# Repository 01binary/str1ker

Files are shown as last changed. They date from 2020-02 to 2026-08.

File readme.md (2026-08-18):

# Str1ker: The Drumming Mech

> [Str1ker](https://www.01binary.us/projects/drumming-robot/) is a human size, open-source mech integrated with Robot Operating System.

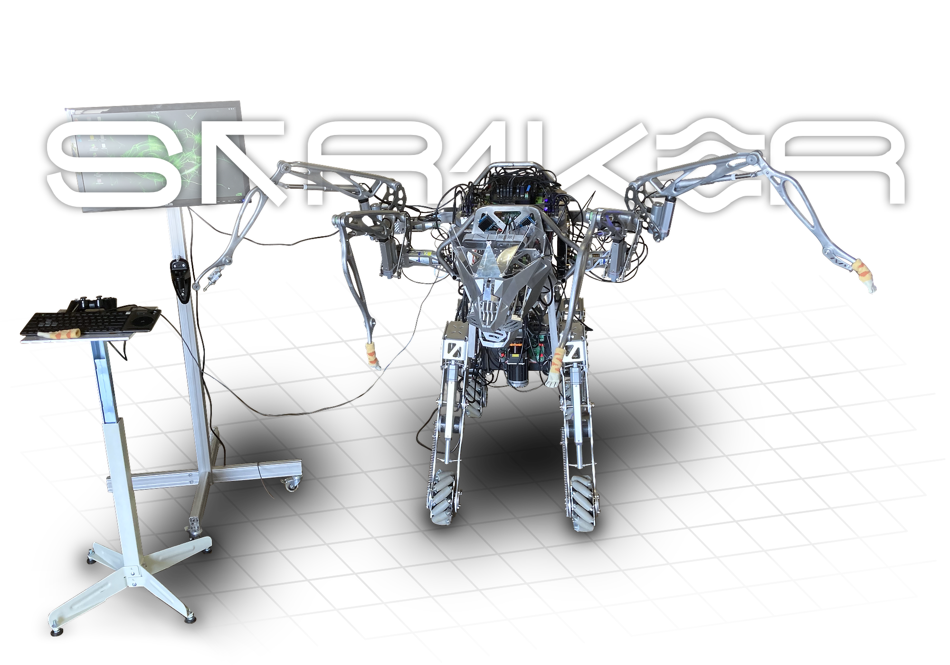
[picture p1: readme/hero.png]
body


## Overview

Striker is a human-scale teleoperated mech built with metal casting, CNC machining, 3D printing, sheet metal parts, tube frame chassis, and pre-made components.

This open-source educational project features custom electronics and [Robot Operating System](https://www.ros.org/) integration, demonstrating how to design and build a large robot that combines mobility, sensing, and manipulation.

> See the [presentation](https://docs.google.com/presentation/d/125Y3McedITN_gVbnEh7SqTWY80QppUtimkaTmMLYEUg/edit?usp=sharing) about the robot at August 2026 [Portland Area Robotics Society](https://portlandrobotics.org/home.php?link_id=1) meeting.

| | | |
|-|-|-|
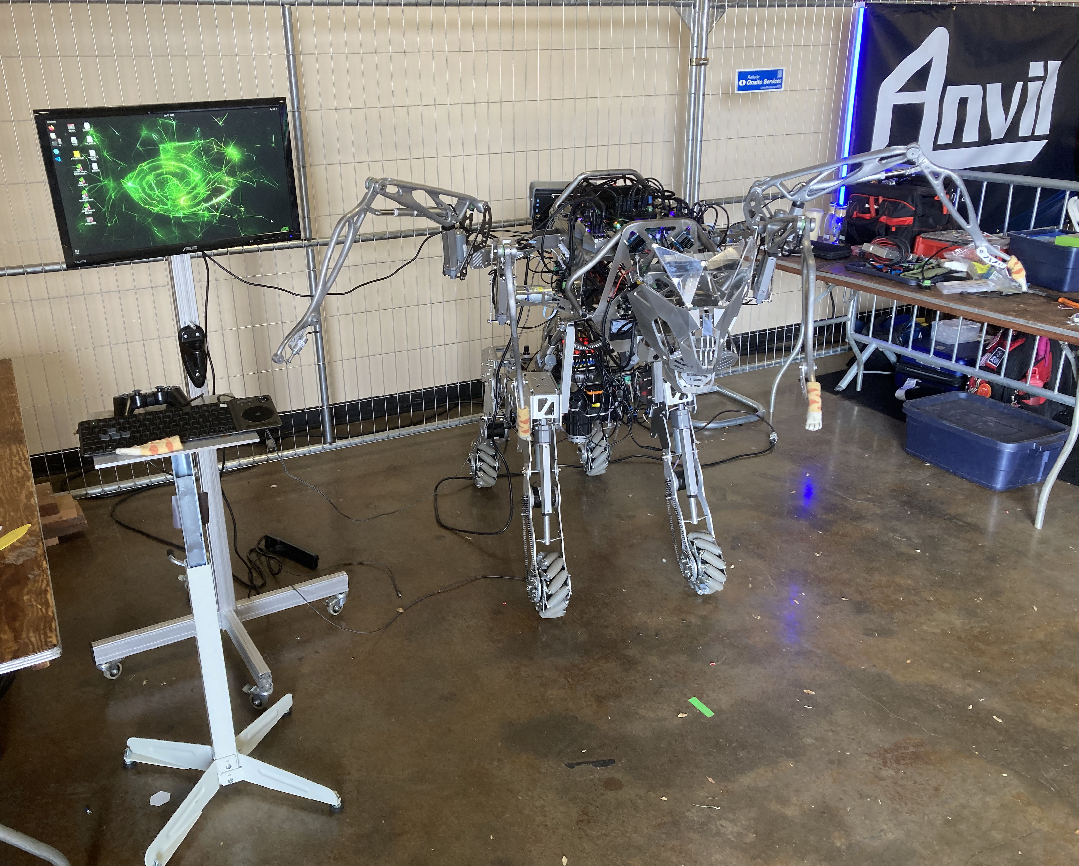
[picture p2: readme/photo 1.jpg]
Front of the robot
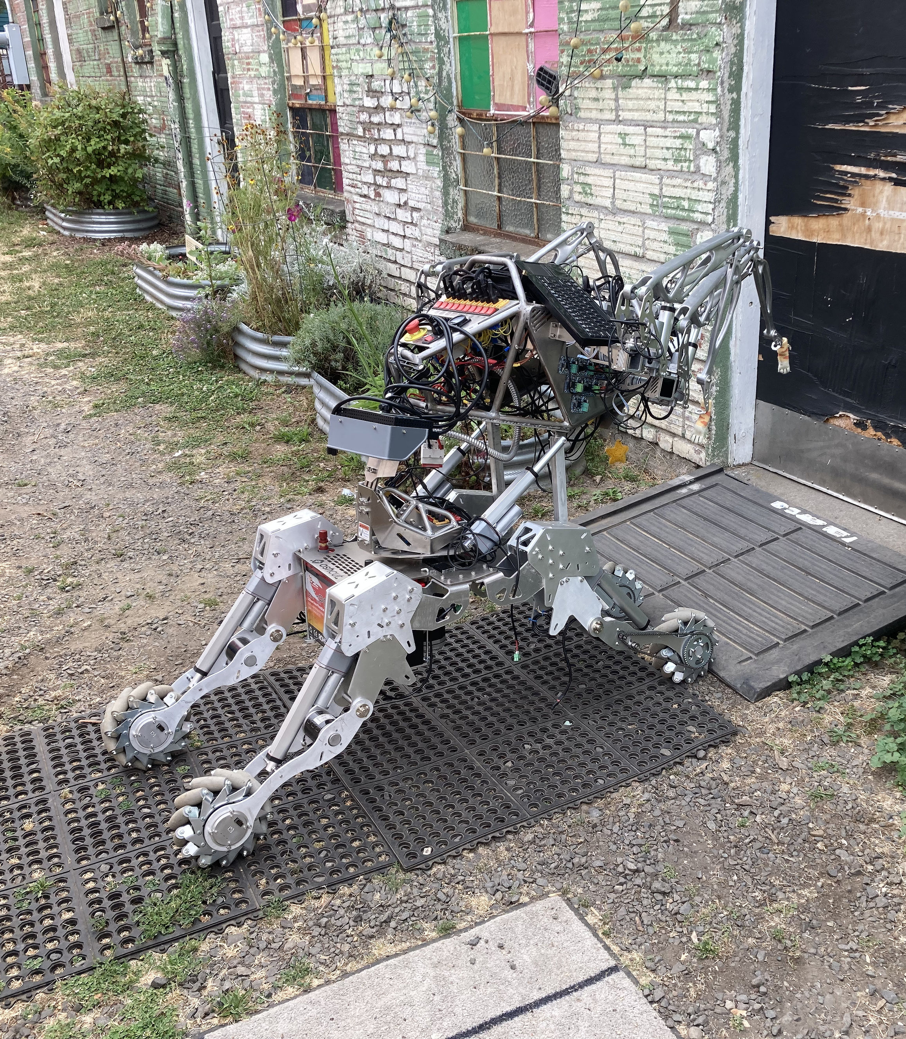
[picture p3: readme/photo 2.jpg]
Robot rolling up a ramp
||Back of the robot||

The robot moves on a mecanum base, articulates its head and arms, and visualizes live lidar and RGB-D perception in Robot Visualization tool ([RViz](https://wiki.ros.org/rviz/Tutorials)).

The arms terminate in percussive end-effectors, designed for future live drum performance.

More details on [my blog](https://www.01binary.us/projects/drumming-robot/) and media on [instagram](https://www.instagram.com/01binaryus/). Say hello at the next [Portland Area Robotics Society](https://portlandrobotics.org/home.php?link_id=1) monthly meetup!

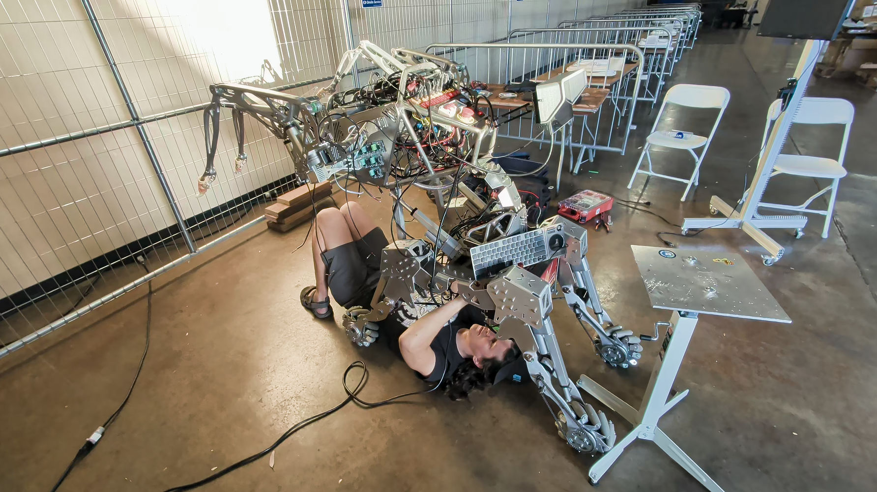
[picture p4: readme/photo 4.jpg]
Maintaining robot at Open Sauce


## Details

### Mechanical Design

[Autodesk Inventor mechanical parts](./cad) available in `./cad`.

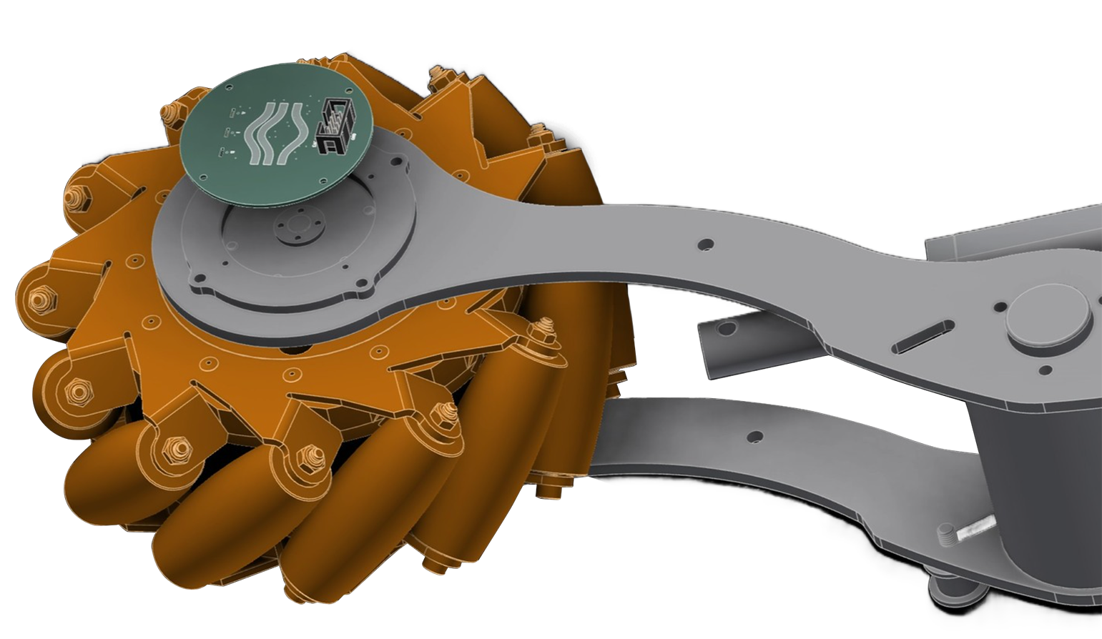
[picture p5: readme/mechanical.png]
mechanical


### Electrical Design

[KiCad schematics and boards](./boards/) available in `./boards`.

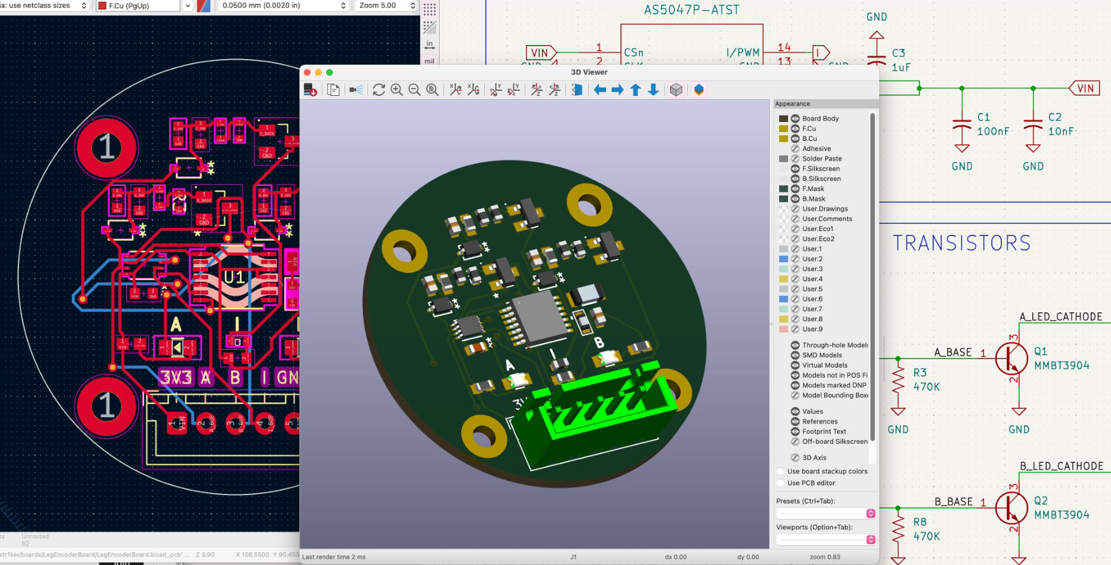
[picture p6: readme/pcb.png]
pcb


### Fabrication

The arms were cast out of Aluminum 356 in the metal foundry at [Ctrl^H Hackerspace](https://pdxhackerspace.org/index.html) and welded together by [skorndaap](https://www.instagram.com/skorndaap/), then polished.

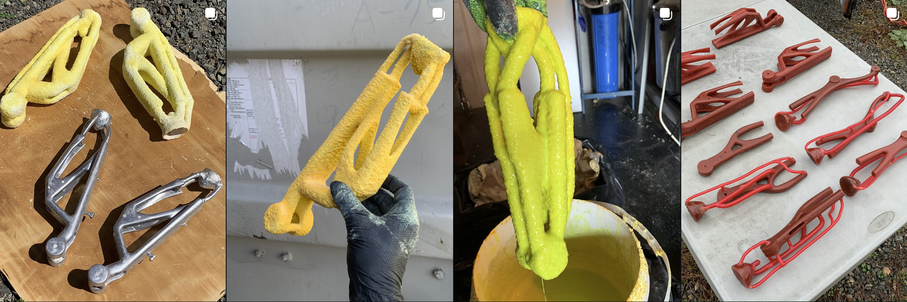
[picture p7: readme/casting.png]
casting


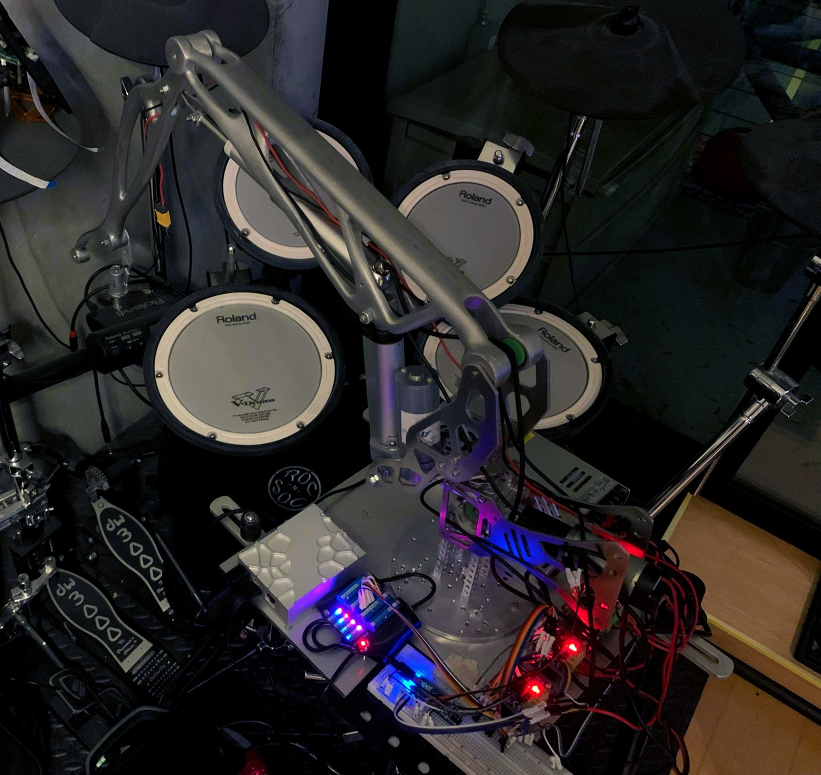
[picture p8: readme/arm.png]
arm


Tube frame chassis welding by [skorndaap](https://www.instagram.com/skorndaap/).

aframem

The CNC, sheet metal, tube frame, and 3D-printed parts were ordered from [Xometry](https://www.xometry.com/) online service.

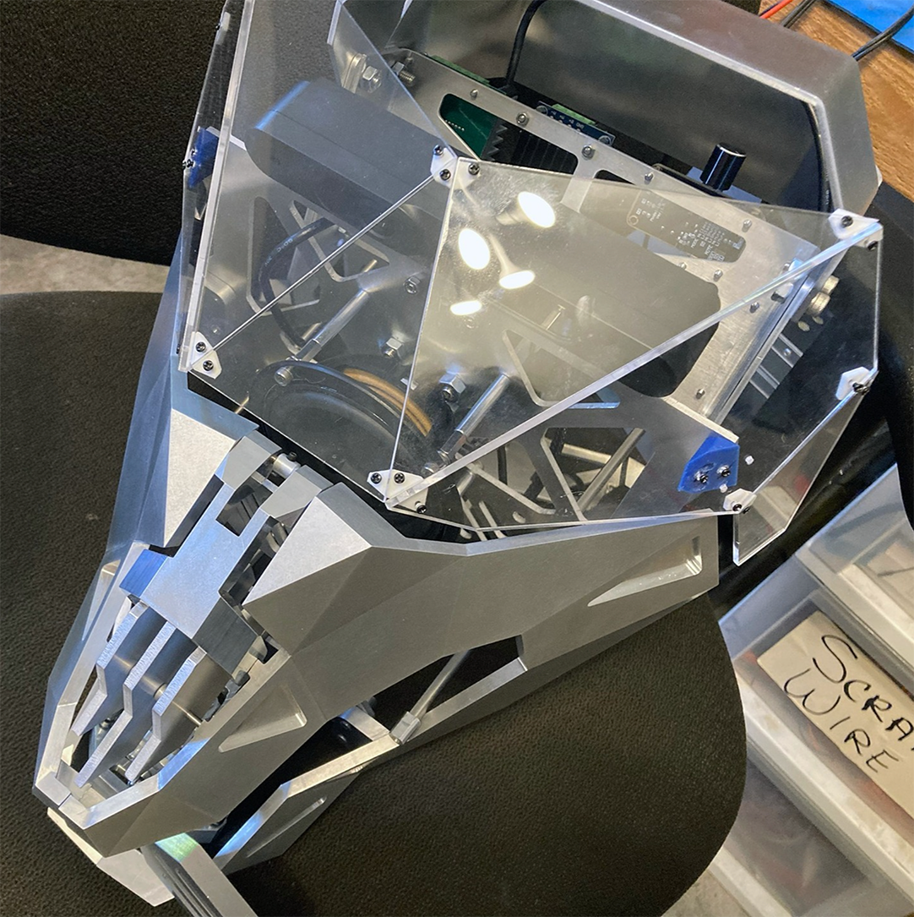
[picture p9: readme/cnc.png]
cnc


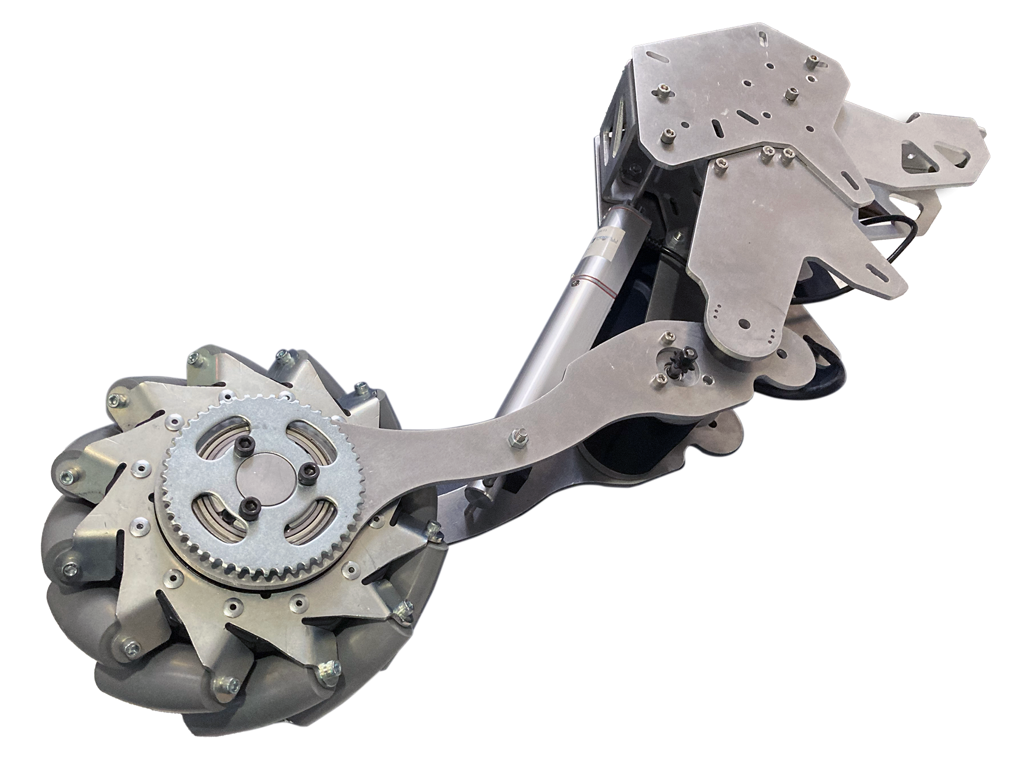
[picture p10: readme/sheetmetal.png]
sheet metal


The PCB's were ordered from [JLCPCB](https://jlcpcb.com/) using JLCPCB KiCad plugin.

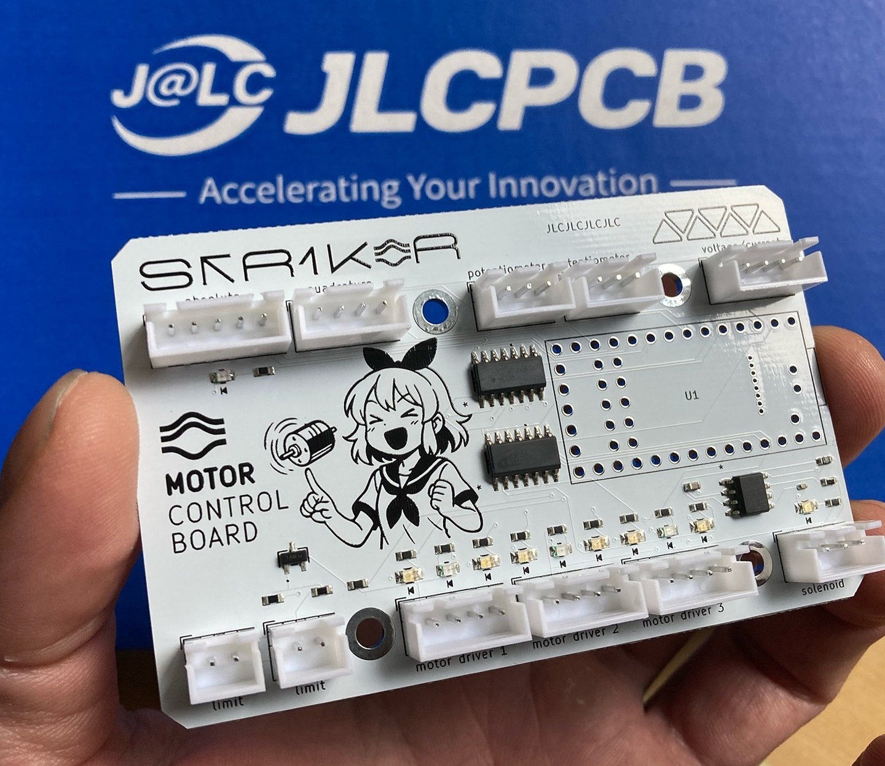
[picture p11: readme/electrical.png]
electrical


Pre-made components sourced from [GoBilda](https://www.gobilda.com/), [Pololu](https://www.pololu.com/), [McMaster-Carr](https://www.mcmaster.com/), [Robot Shop](https://www.robotshop.com/), and Amazon.

### Software

- [Ubuntu 20.04](https://wiki.ros.org/noetic/Installation/Ubunt)
- [ROS Noetic](https://wiki.ros.org/noetic)
- [MoveIt](https://moveit.ai/)
- [ROS Control](./src/hardware/hardware.h)
- [Inverse Kinematics solver](./src/plugins/)
- [PID controller](./src/drivers/arm/pid.h)
- [ROS](./src) and [ROS Serial](./src/drivers/) nodes

### Hardware

- [Teensy 4.0](https://www.sparkfun.com/teensy-4-0.html) MCUs for arms, body and legs
- [Weidian](https://www.amazon.com/dp/B0BTVN6V7W) industrial mini PC for high-level control
- [Intel NUC 11](https://www.amazon.com/dp/B09PRL9V2F) for teleoperation & simulation

## System Requirements

The high-level controllers (Ubuntu 20.04/ROS Noetic) can run on any [mini PC](https://www.amazon.com/s?k=mini+pc), [NUC](https://www.amazon.com/s?k=NUC), a low-end Single Board Computer (SBC) like [Raspberry Pi](https://www.amazon.com/Raspberry-Model-2019-Quad-Bluetooth/dp/B07TD43PDZ/) or a high-end SBC like [Latte Panda 3 Delta](https://www.amazon.com/LattePanda-864-Pocket-Sized-Windows-Single-Computer/dp/B0C6TCP3MN).

The low-level serial nodes that run motors and sensors were designed for Arduino Mega, and are currently being ported to [Teensy 4.0](https://www.sparkfun.com/teensy-4-0.html) because its more powerful specs make it a better choice for robotics.

Teleoperation and simulation requires 3D visualization software like [RViz](https://wiki.ros.org/rviz) and [Gazebo](https://gazebosim.org/home), which [like NVidia cards](https://wiki.ros.org/simulator_gazebo/SystemRequirements).

## Setup

Follow the [official guide](https://wiki.ros.org/noetic/Installation/Ubuntu) to install ROS Noetic and [configure the ROS environment](https://wiki.ros.org/ROS/Tutorials/InstallingandConfiguringROSEnvironment).

Clone the projects:

```
mkdir -p ~/catkin_ws/src
cd ~/catkin_ws/src

git clone https://github.com/01binary/str1ker.git
git clone https://github.com/01binary/str1ker_moveit_config.git

cd ./str1ker
git sparse-checkout init --cone
git sparse-checkout set .vscode src config launch description msg
```

## Install Packages from Source

Follow the [official guide](https://moveit.ai/install/source/) to build MoveIt from source using `catkin_ws` as the workspace name instead of `moveit_ws`.

Prepare Gazebo plugins to be built from source:

```
cd ~/catkin_ws/src
git clone https://github.com/roboticsgroup/roboticsgroup_gazebo_plugins
```

## Install Packages

```
cd ~/catkin_ws/src
rosdep install -y --from-paths . --ignore-src --rosdistro noetic
```

## Build

To invoke the build command while in `~/catkin_ws` use `catkin_make` with no parameters. Otherwise use `-C` to specify the workspace directory:

```
catkin_make -C ~/catkin_ws
```

To build only this package and its dependencies:

```
catkin_make --only-pkg-with-deps str1ker
```

To build only this package:

```
catkin_make --pkg str1ker
```

To clear the build filter:

```
catkin_make -DCATKIN_WHITELIST_PACKAGES=""
```

To switch between Debug and Release

```
catkin_make -DCMAKE_BUILD_TYPE=Debug | Release
```

## Environment

One-time setup after the first build.

```
catkin_make install
source /opt/ros/noetic/setup.bash

echo "source /opt/ros/noetic/setup.bash" >> ~/.bashrc
source ~/.bashrc
```

## Upload

The low-level hardware is handled by an Arduino ROS node in `src/drivers/arm.ino`.

To build it, first generate ROS message headers for Arduino:

```
sudo apt-get install ros-${ROS_DISTRO}-rosserial-arduino
sudo apt-get install ros-${ROS_DISTRO}-rosserial

rosrun rosserial_arduino make_libraries.py ~/Arduino/libraries
```

> If you installed Arduino IDE as a *snap* plugin, Arduino libraries are likely in `~/snap/arduino` (the exact location is specific to your system).

Compile and upload the ROS node. The default launch configuration in `robot.launch` will connect to `/dev/ttyACM0` automatically.

### VSCode + Arduino CLI

This workspace includes VSCode tasks for compiling and uploading the Teensy firmware without Arduino IDE 2.

Install `arduino-cli`:

```bash
curl -fsSL https://raw.githubusercontent.com/arduino/arduino-cli/master/install.sh | BINDIR="$HOME/.local/bin" sh
arduino-cli version
```

Then in VSCode:

1. Open the Command Palette and run `C/C++: Select a Configuration...`
2. Pick `Arduino Teensy 4.0`
3. Run `Tasks: Run Task`
4. Use `Arduino: Compile Arm` or `Arduino: Upload Arm`

The checked-in VSCode configuration targets `teensy:avr:teensy40` on `/dev/ttyACM0` and uses the PJRC package index through `.vscode/arduino-cli.yaml`.

## Launch

### Hardware

To launch only the serial bridge to the arm firmware:

```
roslaunch str1ker arms.launch
```

To launch only the serial bridge to the main board firmware:

```
roslaunch str1ker main.launch
```

### Controllers

To launch ROS control nodes (URDF + controllers + state publisher):

```
roslaunch str1ker controllers.launch
```

### Full Stack

To launch both high-level and low-level nodes:

```
roslaunch str1ker robot.launch
```

### PrimeSense Carmine 1.09

To launch Carmine with OpenNI2 (recommended on ROS Noetic):

```
roslaunch str1ker vision.launch
```

To use legacy OpenNI instead:

```
roslaunch str1ker vision.launch use_openni2:=false
```

### Laser Scanner (Hokuyo UTM-30LX)

Install the Hokuyo ROS driver:

```
sudo apt-get install -y ros-${ROS_DISTRO}-urg-node
```

The default launch path uses the stable built-in udev symlink under `/dev/serial/by-id`.

If you still want a custom short alias (for example `/dev/str1ker_laser`), create one with:

```
# Example when Hokuyo appears as /dev/ttyACM0
./scripts/alias.sh /dev/ttyACM0 str1ker_laser --install
```

To launch the laser scanner driver:

```
roslaunch str1ker laserscan.launch
```

If you want to bypass by-id and use the current kernel device path:

```
roslaunch str1ker laserscan.launch serial_port:=/dev/ttyACM0
```

### Mecanum Legs

The legs firmware runs as a rosserial Arduino node and subscribes to `cmd_vel`
using `geometry_msgs/Twist` (`linear.x`, `linear.y`, and `angular.z`).

To launch the serial bridge:

```
roslaunch str1ker legs.launch serial_port:=/dev/ttyACM0
```

Quick forward-motion smoke test:

```
rostopic pub -r 10 /cmd_vel geometry_msgs/Twist "{linear: {x: 0.2, y: 0.0, z: 0.0}, angular: {x: 0.0, y: 0.0, z: 0.0}}"
```

### Teleoperation

To teleoperate the robot:

```
roslaunch str1ker_moveit_config demo.launch
```

### Simulation

To simulate the robot:

```
roslaunch str1ker_moveit_config gazebo.launch
```

### Configuration

The low-level configuration is in YAML format at [config](./config/).

To launch the MoveIt wizard for custom robot arm setup:

```
roslaunch moveit_setup_assistant setup_assistant.launch
```

## Logging

Logging level can be specified in `$ROS_ROOT/config/rosconsole.config`, either globally or for a specific package.

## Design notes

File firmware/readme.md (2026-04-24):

To compile Arduino firmware, symlink this folder into your Arduino libraries folder.
This effectively creates a private library for the project.

```bash
ln -s /repo-path/firmware ~/Arduino/libraries/str1ker
```

Arduino adds the library directory itself to the include path, so includes
should reference the header name directly.

Use:

```c++
#include <firmware.h>
```

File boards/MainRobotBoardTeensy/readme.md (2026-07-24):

# Main Robot Board

A board that controls robot head & body and measures voltage/current/battery charge.

+ Head Pan/Tilt
+ Torso Pan/Tilt
+ Mouth Movement
+ Voltage and Current Sensing

## Modules

The following components are placed onto the board as modules:

|Module|Function|
|-|-|
|[Teensy 4.1](https://www.sparkfun.com/teensy-4-1.html)|[ROS](https://www.ros.org/) Node|
|[ACS37220 Current Sensor 100A](https://www.pololu.com/product/5295)|Bus Current Sensing|
|[SSD1306 OLED Displays](https://www.amazon.com/dp/B00O2LKEW2)|Monochrome 0.96" 128x64 Voltage/Current/Power displays|
|[B10 1B4PG3Y2R](https://www.amazon.com/dp/B0C9QGMGFB)|Battery Charge Meter|
## Devices

The following external components are connected to the board via JST-XH locking connectors:

|Device|Function|
|-|-|
|[TB6600HG Stepper Motor Driver](https://www.amazon.com/dp/B01N6AIEQT)|Head Pan Motor|
|`4x` [Mini IBT Motor Driver](https://www.aliexpress.us/item/2251832603816751.html)|`2x` Head Tilt Motor Driver, `2x` Torso Tilt Motor Driver|
|`2x` Hollow Shaft Potentiometers|Head Tilt Encoder, Torso Tilt Encoder|
|[PerfectPass 56Kg Servo](https://www.amazon.com/dp/B09Y4NZJBJ)|Mouth Movement|
|[CPM-MCVC-3441S-RLN](https://teknic.com/model-info/CPM-MCVC-3441S-RLN/?model_voltage=75VDC)|Torso Pan Integrated Motor Driver

## Buses

|Bus|Device|Address
|-|-|-|
|`I2C`|SSD1306 voltage, current, and power meter displays|`0x3C`, `0x3D`|

## Pins

|Pin|Function
|-|-|
| `D14/A0`  | `ACS37220` Current Sensor `VOUT`
| `D15/A1`  | Head Tilt Potentiometer `SIG`
| `D16/A2`  | Torso Tilt Potentiometer `SIG`
| `D17/A3`  | Voltage Sense `SIG`
| `D19` | I2C `SCL` (SSD1306 x2)
| `D18` | I2C `SDA` (SSD1306 x2)
| `D0` | `TB6600` Head Pan Stepper Driver `EN`
| `D1` | `TB6600` Head Pan Stepper Driver `DIR`
| `D2` | `TB6600` Head Pan Stepper Driver `PUL`
| `D3` | `CPM-MCVC-3441S-RLN` Torso Motor `EN`
| `D4` | `CPM-MCVC-3441S-RLN` Torso Motor `DIR` (A)
| `D5` | `CPM-MCVC-3441S-RLN` Torso Motor `PWM` (B)
| `D7` | Head Tilt Motor Driver 1 `EN`
| `D8` | Head Tilt Motor Driver 2 `EN`
| `D20` | Torso Tilt Motor Driver 1 `EN`
| `D21` | Torso Tilt Motor Driver 2 `EN`
| `D9` | Head Tilt Motor Driver 1 `LPWM`
| `D10` | Head Tilt Motor Driver 1 `RPWM`
| `D11` | Head Tilt Motor Driver 2 `LPWM`
| `D12` | Head Tilt Motor Driver 2 `RPWM`
| `D22` | Torso Tilt Motor Driver 1 `LPWM`
| `D23` | Torso Tilt Motor Driver 1 `RPWM`
| `D28` | Torso Tilt Motor Driver 2 `LPWM`
| `D29` | Torso Tilt Motor Driver 2 `RPWM`
| `D24` | Battery Level Meter `LED1` (Lowest Charge)
| `D25` | Battery Level Meter `LED2`
| `D26` | Battery Level Meter `LED3`
| `D27` | Battery Level Meter `LED4`
| `D30` | Battery Level Meter `LED5`
| `D31` | Battery Level Meter `LED6`
| `D32` | Battery Level Meter `LED7`
| `D33` | Battery Level Meter `LED8`
| `D34` | Battery Level Meter `LED9`
| `D35` | Battery Level Meter `LED10` (Highest Charge)
| `D36` | PerfectPass Servo `SIG`

## ROS Interface

The main-board Teensy is a rosserial node at `115200` baud. Its USB serial
port is reserved for ROS framing; the sketch does not print diagnostic text.

|Topic|Type|Direction|Rate / behavior|
|-|-|-|-|
|`main/command`|`str1ker/MainCommand`|Subscribe|Normalized `[-1, 1]` velocity commands for head pan/tilt and torso pan/tilt, plus mouth position in degrees. Motion stops if commands are absent for 500 ms.|
|`main/power`|`str1ker/PowerState`|Publish|Voltage (V), current (A), and power (W), at 10 Hz.|
|`main/battery`|`sensor_msgs/BatteryState`|Publish|LiFePO4 pack voltage, current, and estimated charge percentage, at 10 Hz.|
|`main/joint_states`|`sensor_msgs/JointState`|Publish|`head_tilt_joint`, `torso_tilt_joint`, and `mouth_joint` positions, at 10 Hz.|

The mouth servo is commanded to 90 degrees during startup. The two
potentiometer positions are currently normalized to `[0, 1]`; calibrate their
ADC endpoints and angular ranges in the firmware before treating them as
radians in a robot model. Head pan and torso pan are omitted from feedback
because this board has no position sensors for those axes.

## Bill of Materials

|Component|Description|
|-|-|
|[150080BS75000](https://www.digikey.com/en/products/detail/w%C3%BCrth-elektronik/)|Blue LED for `LPWM`/`RPWM` activity|
|[XL-1608SURC-06](https://www.lcsc.com/product-detail/C965799.html)|Red LED for `EN` status|
|[RC0603FR-0747RL](https://www.digikey.com/en/products/detail/yageo/rc0603fr-0747rl/727252)|`47R` Series Resistor (PWM channels)|
|[RC0603FR-07150RL](https://www.digikey.com/en/products/detail/yageo/RC0603FR-07150RL/726958)|`150R` Blue LED Resistor|
|[RC0603FR-07470RL](https://www.digikey.com/en/products/detail/yageo/RC0603FR-07470RL/727256)|`470R` Red LED and Battery Bar Segment Resistor|
|[RCG06031K00FKEA](https://www.digikey.com/en/products/detail/vishay-dale/rcg06031k00fkea/4172389)|`1K` Red LED Resistor|
|[RC0603FR-072K2L](https://www.digikey.com/en/products/detail/yageo/RC0603FR-072K2L/727016)|`2.2K` Series Resistor (ADC channels)|
|[CRCW060310K0FKEA](https://www.digikey.com/en/products/detail/vishay-dale/crcw060310k0fkea/1174782)|`10K` Pull-Down Resistor (PWM channels)|
|[0603WAF2202T5E](https://jlcpcb.com/partdetail/32812-0603WAF2202T5E/C31850)|`22K` Voltage Sense Divider Resistor|
|[CRCW0603100KFKEA](https://www.digikey.com/en/products/detail/vishay-dale/crcw0603100kfkea/1174896)|`100K` Pull-Dowh Resistor|
|[CL10B473KB8NNNC](https://www.digikey.com/en/products/detail/samsung-electro-mechanics/cl10b473kb8nnnc/3886721)|`47nF` Capacitor (ADC channels)|
|[SN74HC08DR](https://www.digikey.com/en/products/detail/texas-instruments/sn74hc08dr/276834)|IC Gate|
|[B10 1B4PG3Y2R](https://www.amazon.com/dp/B0C9QGMGFB)|LED Light Bar (Red/Blue/Green) with `DIP-20` Socket (Battery Charge Meter)|
|[AO3400A](https://www.digikey.com/en/products/detail/alpha-omega-semiconductor-inc/ao3400a/1855772)|LED Transistor|
|[TLC555CDR](https://www.digikey.com/en/products/detail/texas-instruments/tlc555cdr/276979)|555 Timer|
|[RC0603FR-07360KL](https://www.digikey.com/en/products/detail/yageo/rc0603fr-07360kl/727183)|555 Timer Resistor `360K`|
|[CC0603JRX7R7BB105](https://www.digikey.com/en/products/detail/yageo/CC0603JRX7R7BB105/7164369)|555 Timer Capacitor `1uF`|
|[C0402C103J4RACTU](https://www.digikey.com/en/products/detail/kemet/C0402C103J4RACTU/411041)|555 Timer Capacitor `0.01uF`|
|[CC0603KRX7R9BB104](https://www.digikey.com/en/products/detail/yageo/cc0603krx7r9bb104/2103082)|`100nF` Voltage Sense Capacitor|
|[74HCT125D,653](https://www.digikey.com/en/products/detail/nexperia-usa-inc/74hct125d-653/763113)|`3.3V` to `5V` Level Shifter|
|[JST_XH_B3B-XH-A](https://www.digikey.com/en/products/detail/jst-sales-america-inc/b3b-xh-a/1651046)|3-pin male receptacle for Head Tilt Potentiometer, Torso Tilt Potentiometer (`3V3`, `SIG`, `GND`), Head Tilt Driver, Torso Tilt Drivers (`LPWM`, `RPWM`, `EN`)|
|[JST_XH_B4B-XH-A](https://www.digikey.com/en/products/detail/jst-sales-america-inc/b4b-xh-a/1651047)|4-pin male receptacle for `TB6600` Driver (`3V3`, `PUL`, `DIR`, `ENA`)|
|[Molex 0702460802](https://www.digikey.com/en/products/detail/molex/0702460802/760180)|2-row 4-pin male receptacle for `CPM-MCVC-3441S-RLN` Driver (`EN+`, `EN-`, `A+`, `A-`, `B+`, `B-`, `ST+`, `ST-`)|
|[Teensy 4.1](https://www.sparkfun.com/teensy-4-1.html)|Teensy 4.1 without Headers|
|[ICM-648-1-GT-HT](https://www.digikey.com/en/products/detail/adam-tech/ICM-648-1-GT-HT/9832918)|Teensy IC DIP Socket, 48P|
|[Needle Headers](https://www.amazon.com/dp/B09WH8N3HX)|Teensy Needle Headers for DIP Socket|
|[ACS37220](https://www.pololu.com/product/5295)|Current Sensor `100A`, `3.3V` Logic|
|2x [SSD1306](https://www.amazon.com/dp/B00O2LKEW2)|Monochrome I2C OLED Displays `3.3V`|

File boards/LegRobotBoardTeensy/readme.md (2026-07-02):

# Leg Robot Board

A board that controls the mobile platform with four mecanum wheels:

+ Leg Actuators
+ Leg Actuator Potentiometers
+ Leg Wheels
+ Leg Wheel Encoders
+ 9-DOF IMU
+ Enabled and PWM activity LEDs
+ Wheel Speed 7-Segment LED Indicators

## Modules

The following components are placed onto the board as modules:

|Module|Function|
|-|-|
|[Teensy 4.1](https://www.pjrc.com/store/teensy41.html)|[ROS](https://www.ros.org/) Node|
|[Adafruit 9-DOF IMU](https://www.adafruit.com/product/2472)|[TF2](https://wiki.ros.org/tf2) Transform|

## Devices

The following external components are connected to the board via `JST-XH` locking connectors:

|Device|Function|
|-|-|
|8x [IBT2 Motor Drivers](https://www.amazon.com/2-Piece-High-Power-Limiting-Function-Suitable/dp/B0DXKXKYRK)|Wheel Motor Drivers, Leg Actuator Drivers (`8` pin IDC connector: `3V3`, `GND`, `L_EN`, `R_EN`, `LPWM`, `RPWM`, `L_IS`, `R_IS`)|
|4x [Feedback Rod Linear Actuator](https://www.firgelliauto.com/products/feedback-rod-actuator?variant=2632742851) Potentiometers|Leg Actuator Potentiometers (`3` pin JST-XH connector: `3V3`, `SIG`, `GND`)|
|4x [Leg (Wheel) Encoder Board](../LegEncoderBoard/readme.md)|Wheel Encoders (`8` pin IDC connector: `A`, `B`, `I`, `3V3`, and four `GND`'s|

## Functionality

### PWM

There are four legs and each has two motors: a linear lift actuator and a brushed DC motor that runs the wheel.

Each PWM channel gets its own `EN` (Enabled) signal. The current sense signals (`L_IS`, `R_IS`) are included in the connector layout and sent over the wire, but not used anywhere on the board because there aren't enough pins for them. A multiplexer can be added later if the signals are desired.

### ADC

The linear lift actuators have built-in multi-turn potentiometers. These are routed to Teensy `ADC` pins.

### Quadrature

The [wheel encoders](../LegEncoderBoard/readme.md) are connected to each of the four wheels, outputting `A`, `B`, and `I` pulses counting rotations (`1000` pulses per revolution).

### Number Displays

Four 7-segment common anode LED number displays with decimal points display the speed of each wheel from `0.0` to `1.0`. They are driven by an LED multiplexer.

The LED multiplexer is mapped to four 2-digit LED displays with decimal point as follows:

| Display function | `IS31FL3730` pins |
| --- | --- |
| Digit common anodes | `SW1–SW8` |
| Segments A, B, C, D, E, F, G, DP | `CS1–CS8` |

The [3621BH](https://www.amazon.com/uxcell-Common-Segment-Display-Digital/dp/B07GTRS9L2) common-anode LED displays have the following pin footprint:

| |1|2|3|4|5|
|-|-|-|-|-|-|
|1|`COM0`|`B`|`C`|`E`|`D`|
|2|`G`|`DP`|`A`|`F`|`COM1`|

The digit segments are mapped as follows:

|Digit|Segments
|-|-|
|digit|`A` - Top of upper square<br>`F` - Left of upper square<br>`B` - Right of upper square<br>`G` - Link of both squares<br>`E` - Left of lower square<br>`C` - Right of lower square<br>`D` - Bottom of lower square<br>`DP` - Decimal point

## Pin Mapping

This board is essentially a shield. Labeled locking connectors are provided for all of the devices, PWM enabled/activity is indicated by LEDs, and wheel speeds are indicated by number displays.

| Pin | Function | Group |
| --- | --- | --- |
| `A16` | Actuator 1 Potentiometer `SIG` | Front Left Leg (Actuator) |
| `D32` | Quadrature Encoder 1 `A` | Front Left Leg (Wheel) |
| `D33` | Quadrature Encoder 1 `B` | Front Left Leg (Wheel) |
| `D22` | Quadrature Encoder 1 `Index` | Front Left Leg (Wheel) |
| `D26` | Motor Driver 1 `EN` | Front Left Leg (Wheel) |
| `D27` | Motor Driver 2 `EN` | Front Left Leg (Actuator) |
| `D0` | Motor Driver 1 `RPWM` | Front Left Leg (Wheel) |
| `D1` | Motor Driver 1 `LPWM` | Front Left Leg (Wheel) |
| `D2` | Motor Driver 2 `RPWM` | Front Left Leg (Actuator) |
| `D3` | Motor Driver 2 `LPWM` | Front Left Leg (Actuator) |
| `A17` | Actuator 2 Potentiometer `SIG` | Front Right Leg (Actuator)|
| `D34` | Quadrature Encoder 2 `A` | Front Right Leg (Wheel) |
| `D35` | Quadrature Encoder 2 `B` | Front Right Leg (Wheel) |
| `D23` | Quadrature Encoder 2 `Index` | Front Right Leg (Wheel) |
| `D28` | Motor Driver 3 `EN` | Front Right Leg (Wheel) |
| `D29` | Motor Driver 4 `EN` | Front Right Leg (Actuator)|
| `D4` | Motor Driver 3 `RPWM` | Front Right Leg (Wheel) |
| `D5` | Motor Driver 3 `LPWM` | Front Right Leg (Wheel) |
| `D6` | Motor Driver 4 `RPWM` | Front Right Leg (Actuator)|
| `D7` | Motor Driver 4 `LPWM` | Front Right Leg (Actuator)|
| `A2` | Actuator 3 Potentiometer `SIG` | Rear Left Leg (Actuator)  |
| `D36` | Quadrature Encoder 3 `A` | Rear Left Leg (Wheel) |
| `D37` | Quadrature Encoder 3 `B` | Rear Left Leg (Wheel) |
| `D24` | Quadrature Encoder 3 `Index` | Rear Left Leg (Wheel) |
| `D30` | Motor Driver 5 `EN` | Rear Left Leg (Wheel) |
| `D31` | Motor Driver 6 `EN` | Rear Left Leg (Actuator)  |
| `D8` | Motor Driver 5 `RPWM` | Rear Left Leg (Wheel) |
| `D9` | Motor Driver 5 `LPWM` | Rear Left Leg (Wheel) |
| `D10` | Motor Driver 6 `RPWM` | Rear Left Leg (Actuator)  |
| `D11` | Motor Driver 6 `LPWM` | Rear Left Leg (Actuator)  |
| `A3` | Actuator 4 Potentiometer `SIG` | Rear Right Leg (Actuator) |
| `D38` | Quadrature Encoder 4 `A` | Rear Right Leg (Wheel) |
| `D39` | Quadrature Encoder 4 `B` | Rear Right Leg (Wheel) |
| `D25` | Quadrature Encoder 4 `Index` | Rear Right Leg (Wheel) |
| `D20` | Motor Driver 7 `EN` | Rear Right Leg (Wheel) |
| `D21` | Motor Driver 8 `EN` | Rear Right Leg (Actuator) |
| `D12` | Motor Driver 7 `RPWM` | Rear Right Leg (Wheel) |
| `D13` | Motor Driver 7 `LPWM` | Rear Right Leg (Wheel) |
| `D14` | Motor Driver 8 `RPWM` | Rear Right Leg (Actuator) |
| `D15` | Motor Driver 8 `LPWM` | Rear Right Leg (Actuator) |
| `A5` | I2C `SCL` | IMU, LED Driver |
| `A4` | I2C `SDA` | IMU, LED Driver |

## Buses

|Device|Bus|Address
|-|-|-|
|IMU|I2C|`0x28` (`ADR` tied to `GND` to set address)|
|IS31FL3730|I2C|`0x74`|

## Bill of Materials

|Component|Description|
|-|-|
|[IS31FL3730](https://www.digikey.com/en/products/detail/lumissil-microsystems/IS31FL3730-QFLS2-TR/5319756)|LED Driver/Multiplexer
|[CL3621BH](https://www.amazon.com/dp/B07GTQTD8S)|LED Displays (2-Digit, 7-Segment, 10-Pin Common Anode) for Wheel Speeds
|[XL-1608SURC-06](https://www.lcsc.com/product-detail/C965799.html)|Red LED for `EN` signals|
|[150080BS75000](https://www.digikey.com/en/products/detail/w%C3%BCrth-elektronik/)|Blue LED for `LPWM`/`RPWM` signals|
|[RC0603FR-07150RL](https://www.digikey.com/en/products/detail/yageo/RC0603FR-07150RL/726958)|`150 Ohm` LED Resistor|
|[RC0603FR-07470RL](https://www.digikey.com/en/products/detail/yageo/RC0603FR-07470RL/727256)|`470R` Red LED Resistor|
|[RCG06031K00FKEA](https://www.digikey.com/en/products/detail/vishay-dale/rcg06031k00fkea/4172389)|`1K` LED Resistor|
|[RC0603FR-072K2L](https://www.digikey.com/en/products/detail/yageo/rc0603fr-072k2l/727016)|`2.2K` Series Resistor (ADC channels)|
|[CR0603-FX-4701ELF](https://www.digikey.com/en/products/detail/bourns-inc/cr0603-fx-4701elf/3740916)|`4.7K` Pull-Up Resistor for LED Multiplexer|
|[CRCW060310K0FKEA](https://www.digikey.com/en/products/detail/vishay-dale/crcw060310k0fkea/1174782)|`10K` 555 Timer Pull-Up Resistor, Transistor Base Resistor|
|[HoAR0603-1/10W-20KR-1%-TCR25](https://jlcpcb.com/partdetail/C5123585)|`20K` LED Driver Current Setting Resistor|
|[CRCW0603100KFKEA](https://www.digikey.com/en/products/detail/vishay-dale/crcw0603100kfkea/1174896)|`100K` Transistor Base Pull-Down Resistor|
|[RC0603FR-07360KL](https://www.digikey.com/en/products/detail/yageo/rc0603fr-07360kl/727183)|`360K` 555 Timer Resistor|
|[C0402C103J4RACTU](https://www.digikey.com/en/products/detail/kemet/C0402C103J4RACTU/411041)|`10nF` 555 Timer Capacitor|
|[CL10B473KB8NNNC](https://www.digikey.com/en/products/detail/samsung-electro-mechanics/cl10b473kb8nnnc/3886721)|`47nF` Decoupling Capacitor (ADC channels)|
|[CC0603KRX7R9BB104](https://www.digikey.com/en/products/detail/yageo/cc0603krx7r9bb104/2103082)|`100nF` IMU Capacitor|
|[CC0603JRX7R7BB105](https://www.digikey.com/en/products/detail/yageo/CC0603JRX7R7BB105/7164369)|`1uF` 555 Timer Capacitor|
|[SN74HC08DR](https://www.digikey.com/en/products/detail/texas-instruments/sn74hc08dr/276834)|IC Gate|
|[MMBT3904LT1G](https://www.digikey.com/en/products/detail/onsemi/MMBT3904LT1G/919601)|LED Transistor|
|[TLC555CDR](https://www.digikey.com/en/products/detail/texas-instruments/tlc555cdr/276979)|555 Timer|
|[JST_XH_B3B-XH-A](https://www.digikey.com/en/products/detail/jst-sales-america-inc/b3b-xh-a/1651046)|Actuator Potentiometers (`3V3`, `SIG`, `GND`)|
|[Molex 0702460802](https://www.digikey.com/en/products/detail/molex/0702460802/760180)|Motor Drivers (`LPWM`, `RPWM`, `L_EN`, `R_EN`, `L_IS`, `R_IS`, `3V3`, `GND`)|
|[Teensy 4.1](https://www.sparkfun.com/teensy-4-1.html)|Teensy 4.1 without Headers|
|[ICM-648-1-GT-HT](https://www.digikey.com/en/products/detail/adam-tech/ICM-648-1-GT-HT/9832918)|Teensy IC DIP Socket, 48P|
|[Needle Headers](https://www.amazon.com/dp/B09WH8N3HX)|Teensy Needle Headers for DIP Socket|
|[DIP Socket 10 pin](https://www.amazon.com/dp/B0FVDT8JGV)|LED number displays IC socket

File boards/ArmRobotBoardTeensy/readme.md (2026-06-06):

# Arm Motor Control Board

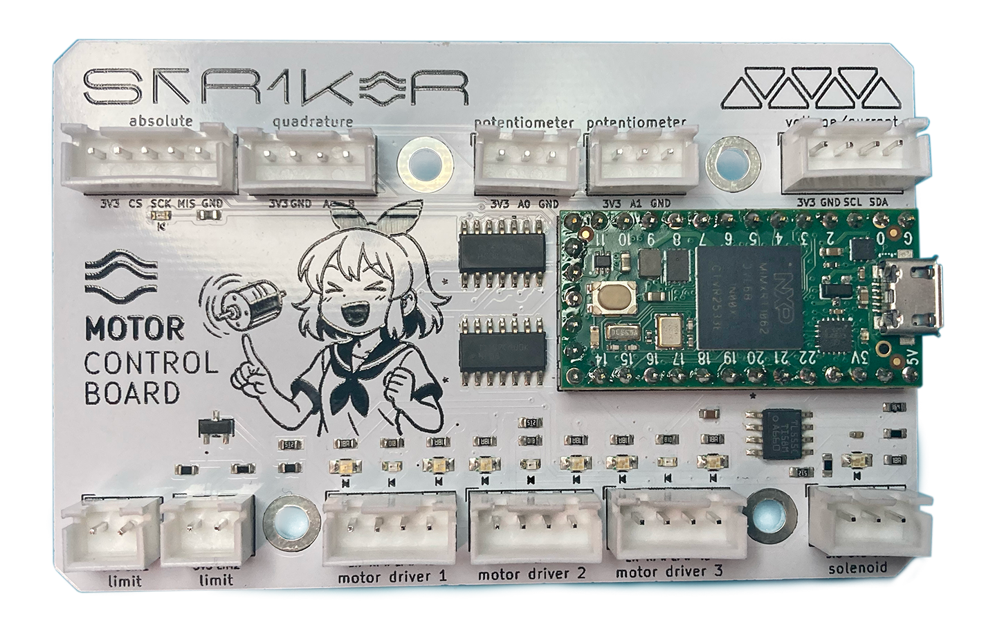
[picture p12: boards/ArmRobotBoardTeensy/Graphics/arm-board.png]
board


## Hardware

A Teensy 4.0-based board that controls one 3-degree of freedom (DoF) robot arm with three motors and an end-effector solenoid.

+ The first joint has a digital absolute encoder (AS5045 on SPI bus, see the [custom encoder board](../ArmEncoderBoard/)) and a relative encoder (A/B quadrature interrupt pins), in addition to two limit switches that automatically cut off the "enabled" signal for the first [Mini IBT](https://www.amazon.com/L6201P-Module-H-Bridge-Control-12V-48V/dp/B09N7L9TLB) motor driver.
+ The other two joints have potentiometers and linear actuators with built-in limit switches connected to the remaining two [Mini IBT](https://www.amazon.com/L6201P-Module-H-Bridge-Control-12V-48V/dp/B09N7L9TLB) motor drivers.
+ All three motor drivers have red *enabled* LEDs and blue *activity* LEDs.
+ The solenoid has a blue *activity* LED that indicates when the signal is being sent to [Adafruit MOSFET Driver](https://www.adafruit.com/product/5648).
+ The SPI connection for the absolute encoder has a red *status* LED.
+ [Adafruit INA260](https://www.adafruit.com/product/4226) Voltage and current sensor is attached to the I2C bus. This is used for system identification and PID controller tuning in the lab (not used in production).

The motor drivers control the following motors and actuators:

|Joint|Description|Motor|
|-|-|-|
|Base|Rotates the arm|[DumaDynamics 56RPM Right Angle Gear Motor w/ 13PPR](https://www.robotshop.com/products/duma-dynamics-56rpm-right-angle-gear-motor-w-13ppr-hall-sensor-encoder)
|Shoulder|Raises or lowers the arm|[Firgelli Classic Rod Linear Actuator](https://www.firgelliauto.com/products/linear-actuators?variant=843909131)
|Elbow|Extends or contracts the arm|[Firgelli Bullet Mini Actuator](https://www.firgelliauto.com/products/bullet-series-mini-actuators?variant=20791982342)

The potentiometers that measure shoulder and elbow joint positions are [NP24HS Series](https://p3america.com/np24hs-series/) from P3 America.

## Software

### Controller

+ All three actuators are PID controlled, with encoders normalized to the travel range.
+ Teensy is configured for 12-bit analog conversion.
+ The PID constants for all three actuators are adjustable via [ROS parameters](../../config/arm.yaml) loaded for the ROS Serial node running on the Teensy 4.0 MCU soldered onto this board.

### ROS Interface

+ Target (set-point) positions for all three joints are subscribed to a ROS queue.
+ Velocities of all three joints are subscribed to a ROS queue (velocity overrides position).
+ Trajectory for the whole arm is subscribed to ROS queue (MoveIt Integration with positions, velocities, and torques).
+ Absolute positions of all three joints are published to ROS queue.
+ Status for encoder, motor drivers, voltage, and current are published to ROS queue with lesser frequency.

## Pin Mapping

This board is essentially a shield, exposing convenient, labeled locking connectors for all of the devices, and indicating PWM enabled/activity with LEDs.

|Pin |Net |Description
|---|---|---
|3V3 |`+3.3V` |Power
|GND |`GND` |Ground
|SPI CS (`D10`) |`CS` |Absolute Encoder CS
|SPI SCK  (`D13`) |`SCK` |Absolute Encoder CK
|SPI MISO (`D12`) |`MISO` |Absolute Encoder DO
|`D9` |`SPIS  ` |Absolute Encoder Status LED
|I2C SCL (`D19`)  |`SCL` |Voltage/Current Sensor SCL
|I2C SDA (`D18`)  |`SDA` |Voltage/Current Sensor SDA
|`D2` |`A` |Quadrature Encoder A
|`D5` |`B` |Quadrature Encoder B
|`A0` (`D14`) |`A0` |Potentiometer 1
|`A1` (`D15`) |`A1` |Potentiometer 2
|`D16` |`PWM1VT` |Motor Driver 1 Current Sense
|`D0` |`PWM1ENSIG`|Motor Driver 1 Enabled
|`D1` |`RPWM1` |Motor Driver 1 RPWM
|`D3` |`LPWM1` |Motor Driver 1 LPWM
|`D4` |`PWM2VT` |Motor Driver 2 Current Sense
|`D6` |`PWM2EN` |Motor Driver 2 Enabled
|`D7` |`RPWM2` |Motor Driver 2 RPWM
|`D8` |`LPWM2` |Motor Driver 2 LPWM
|`D20` |`PWM3VT` |Motor Driver 3 Current Sense
|`D21` |`PWM3EN` |Motor Driver 3 Enabled
|`D22` |`RPWM3` |Motor Driver 3 RPWM
|`D23` |`LPWM3` |Motor Driver 3 LPWM
|`D17` |`SIG` |Solenoid Driver Signal

## Motor Drivers

There are three external [Mini IBT](https://www.amazon.com/L6201P-Module-H-Bridge-Control-12V-48V/dp/B09N7L9TLB) motor drivers, each with `EN` (enabled), `RPWM` (right PWM velocity), `LPWM` (left PWM velocity) and `VT` (current sense) pins.

Each motor driver has a *status LED* that lights up whenever the driver is enabled (`EN` is `HIGH`).

Each motor driver also has two *activity LEDs* that blink whenever `RPWM` or `LPWM` pins are active. Logic *AND* gates are used along with a 555 timer to blink these activity LEDs whenever a non-zero PWM signal is being sent to these pins.

The 555 timer is configured with two resistors, `10K` and `360K`, for a blink rate of `~2 Hz` (two blinks per second).

The first PWM channel has two normally-open limit switches that cut off the `EN` signal from microcontroller when closed by using a transistor. In this way, even if this PWM channel is enabled by the controller, closing either switch will disable it.

The two linear actuators that control forearm and elbow joints have built-in limit switches but the motor that rotates the arm will happily keep pushing when reaching the limits of its motion, which damages the hardware unnecessarily - these external limit switches solve that problem.

Each motor driver also has a *current sense* pin. These are connected to Teensy ADC pins to read the current of each motor, which is accomplished by placing a `5.1K` resistor to `GND` on current sense lines. The current can be calculated using this formula:

`I = V * 8500 / R` where

+ `I` is the motor current
+ `V` is read voltage from the ADC
+ `R` is the chosen resistor, in this case `5.1K` chosen to produce `3V` on the ADC pin at `5A` (maximum rated) motor current.

Motor drivers are labeled as follows on the schematic:

|Net |Description
|---|---|
|`PWM1EN` |PWM Channel `1` Enabled
|`RPWM1` |PWM Channel `1` RPWM
|`LPWM1` |PWM Channel `1` LPWM
|`PWM1VT` |PWM Channel `1` Current Sense
|`PWM2EN` |PWM Channel `2` Enabled
|`RPWM2` |PWM Channel `2` RPWM
|`LPWM2` |PWM Channel `2` LPWM
|`PWM2VT` |PWM Channel `2` Current Sense
|`PWM3EN` |PWM Channel `3` Enabled
|`RPWM3` |PWM Channel `3` RPWM
|`LPWM3` |PWM Channel `3` LPWM
|`PWM3VT` |PWM Channel `3` Current Sense

## Solenoid

There is one external solenoid connected to [Adafruit MOSFET Driver](https://www.adafruit.com/product/5648) with `VDD` (power), `GND` (ground), and `SIG` (signal) pins. The solenoid driver is enabled when it gets power from Teensy on the `VDD` pin, and gets triggered whenever `SIG` pin is `HIGH`.

The solenoid signal pin has its own activity LED which lights up whenever the solenoid is triggered through the `SIG` pin.

|Net |Description
|---|---|
|`SIG` |Solenoid Trigger

## Absolute Encoder

An external [absolute encoder board](../ArmEncoderBoard/) is attached to Teensy SPI bus with pins `VDD` (power), `CS` (chip select), `SCK` (SPI clock), `MISO` (SPI input), and `GND` (ground).

When the communication with the encoder is initialized successfully, the controller will set pin `D9` to `HIGH`. This pin is connected to a red encoder status LED.

|Net |Description
|---|---|
|`3V3` |Absolute Encoder Power
|`GND` |Absolute Encoder Ground
|`SPIS` |Absolute Encoder Status LED
|`CS` |Absolute Encoder SPI Select
|`SCK` |Absolute Encoder SPI Clock
|`MISO` |Absolute Encoder SPI Output

## Relative Encoder

An external relative encoder is attached to Teensy interruptable pins `D2` and `D5`. Like the absolute encoder, it is powered through Teensy 3.3V and Ground pins.

This encoder is built into the [DumaDynamics](https://www.robotshop.com/products/duma-dynamics-56rpm-right-angle-gear-motor-w-13ppr-hall-sensor-encoder) motor used to rotate the arm.

|Net |Description
|---|---|
|`3V3` |Relative Encoder Power
|`GND` |Relative Encoder Ground
|`A` |Relative Encoder A Channel
|`B` |Relative Encoder B Channel

## Potentiometers

Two external [NP24HS Series](https://p3america.com/np24hs-series/) potentiometers are attached to Teensy pins `A0` and `A1` through locking connectors:

|Net |Description
|---|---|
|`3V3` |Potentiometer Power
|`GND` |Potentiometer Ground
|`A0` |Potentiometer 1 Voltage
|`A1` |Potentiometer 2 Voltage

## Voltage/Current Sensor

An external voltage/current sensor ([Adafruit INA260](https://www.adafruit.com/product/4226)) is attached to Teensy I2C bus with pins `SCL` (I2C Clock) and `SDA` (I2C Data) through a locking connector. This sensor also takes Teensy Power and Ground.

|Net |Description
|---|---|
|`3V3` |Voltage/Current Sensor Power
|`GND` |Voltage/Current Sensor Ground
|`SCL` |Voltage/Current Sensor Clock
|`SDA` |Voltage/Current Sensor Output

# Bill of Materials

|Component|Description|
|-|-|
|[Teensy 4.0](https://www.sparkfun.com/teensy-4-0-headers.html)|MCU
|[NCD0603R1](https://www.lcsc.com/product-detail/C84263.html)|Red LED
|[150080BS75000](https://www.digikey.com/en/products/detail/w%C3%BCrth-elektronik/150080bs75000/4489912)|Blue LED
|[RC0603FR-07150RL](https://www.digikey.com/en/products/detail/yageo/RC0603FR-07150RL/726958)|Blue LED Resistor `150 Ohm`
|[RCG06031K00FKEA](https://www.digikey.com/en/products/detail/vishay-dale/rcg06031k00fkea/4172389)|Red LED Resistor `1K`
|[RC0603FR-075K1L](https://www.digikey.com/en/products/detail/yageo/rc0603fr-075k1l/727268)|Current Sense Resistor `5.1K`
|[CRCW060310K0FKEA](https://www.digikey.com/en/products/detail/vishay-dale/crcw060310k0fkea/1174782)|Pullup Resistor, 555 Timer Resistor `10K`
|[CRCW0603100KFKEA](https://www.digikey.com/en/products/detail/vishay-dale/crcw0603100kfkea/1174896)|Series Resistor `100K`
|[RC0603FR-07360KL](https://www.digikey.com/en/products/detail/yageo/rc0603fr-07360kl/727183)|555 Timer Resistor `360K`
|[SN74HC08DR](https://www.digikey.com/en/products/detail/texas-instruments/sn74hc08dr/276834)|IC Gate
|[SMMBT3904LT1G](https://www.digikey.com/en/products/detail/onsemi/smmbt3904lt1g/3062754)|Transistor
|[TLC555CDR](https://www.digikey.com/en/products/detail/texas-instruments/tlc555cdr/276979)|555 Timer
|[CC0603JRX7R7BB105](https://www.digikey.com/en/products/detail/yageo/CC0603JRX7R7BB105/7164369)|555 Timer Capacitor `1uF`
|[C0402C103J4RACTU](https://www.digikey.com/en/products/detail/kemet/C0402C103J4RACTU/411041)|555 Timer Capacitor `0.01uF` (`100nF`)
|[JST_XH_B5B-XH-A](https://www.digikey.com/en/products/detail/jst-sales-america-inc/b5b-xh-a/1530483)|Absolute Encoder Connector
|[JST_XH_B4B-XH-A](https://www.digikey.com/en/products/detail/jst-sales-america-inc/b4b-xh-a/1651047)|Relative Encoder Connector, Voltage/Current Sensor Connector, PWM connectors
|[JST_XH_B3B-XH-A](https://www.digikey.com/en/products/detail/jst-sales-america-inc/b3b-xh-a/1651046)|Solenoid Connector
|[JST_XH_B2B-XH-A](https://www.digikey.com/en/products/detail/jst-sales-america-inc/b2b-xh-a/1651045)|Limit Switch Connectors
|[Millmax 823-22-010-10-001101](https://www.digikey.com/en/products/detail/digikey-va/823-22-010-10-001101/1146931)|Spring-loaded 2x5 connector for bottom Teensy pins|
|[Millmax 0531-0-15-15-31-27-10-0](https://www.digikey.com/en/products/detail/mill-max-manufacturing-corp/0531-0-15-15-31-27-10-0/4879975)|Pin receptacle connector for side Teensy pins|

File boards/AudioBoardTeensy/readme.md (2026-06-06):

# Audio Board

Displays audio waveform and level meter when the robot talks.

## Components

The following components are used:

|Component|Function|
|-|-|
|[Teensy 4.0](https://www.sparkfun.com/teensy-4-0.html)|MCU
|[SSD1309 OLED Display](https://www.dfrobot.com/product-2521.html)|Audio waveform display
|[Adafruit Sequins](https://www.adafruit.com/product/1792)|Audio level metering

## Buses

|Bus|Devices
|-|-|
|`SPI`|SSD1309

## Pins

|Pin|Function|
|-|-|
|`A0` | Audio input from Voltage Divider
|`D13`| OLED Display `SCK`
|`D12`| OLED Display `DC` (`MISO`)
|`D11`| OLED Display `MOSI`
|`D0` | OLED Display `CS`
|`D1` | OLED Display Reset
|`D2` | LED 1
|`D3` | LED 2
|`D4` | LED 3
|`D5` | LED 4
|`D6` | LED 5

Only a single pin from the TRRS audio jack (stereo audio + mono mic) is used as the audio signal for this board:

|Jack Pin|Description|Function
|-|-|-|
|`4`|Tip|Left audio channel output to Voltage Divider
|`3`|Ring 1|Right audio channel (unconnected)
|`2`|Ring 2|`GND`
|`1`|Sleeve|Mic (unconnected)

> This audio jack was used because it's more commonly in stock by various manufacturers than mono audio jacks or stereo audio jacks with no mic.

## Bill of Materials

|Component|Description|
|-|-|
|[CRCW0603100KFKEA](https://www.digikey.com/en/products/detail/vishay-dale/crcw0603100kfkea/1174896)|Voltage Divider Resistor `100K`
|[CL10A106KP8NNNC](https://www.digikey.com/en/products/detail/samsung-electro-mechanics/cl10a106kp8nnnc/3886850)|Voltage Bias Capacitor `10uF`
|[0603WAF2001T5E](https://www.lcsc.com/product-detail/C22975.html)|Pull-Down Resistor `2K`
|[RCG06031K00FKEA](https://www.digikey.com/en/products/detail/vishay-dale/rcg06031k00fkea/4172389)|Current-Limiting Resistor `1K`
|[54-00174](https://www.digikey.com/en/products/detail/tensility-international-corp/54-00174/12140150)|Audio Jack 3.5mm TRRS (2 Stereo channels and Microphone mono channel which is unused)
|[1792](https://www.digikey.com/en/products/detail/adafruit-industries-llc/1792/5774409)|Adafruit LED Sequins Pink
|[Teensy 4.0](https://www.sparkfun.com/teensy-4-0-headers.html)|Teensy 4.0 with Headers
|[Millmax 0531-0-15-15-31-27-10-0](https://www.digikey.com/en/products/detail/mill-max-manufacturing-corp/0531-0-15-15-31-27-10-0/4879975)|Pin receptacle connector for side Teensy pins|

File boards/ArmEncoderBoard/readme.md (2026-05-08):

# Arm Encoder Board

A custom board that simplifies mounting `AS5045` hall-effect on-axis encoder with 12-bit resolution onto robot joints.

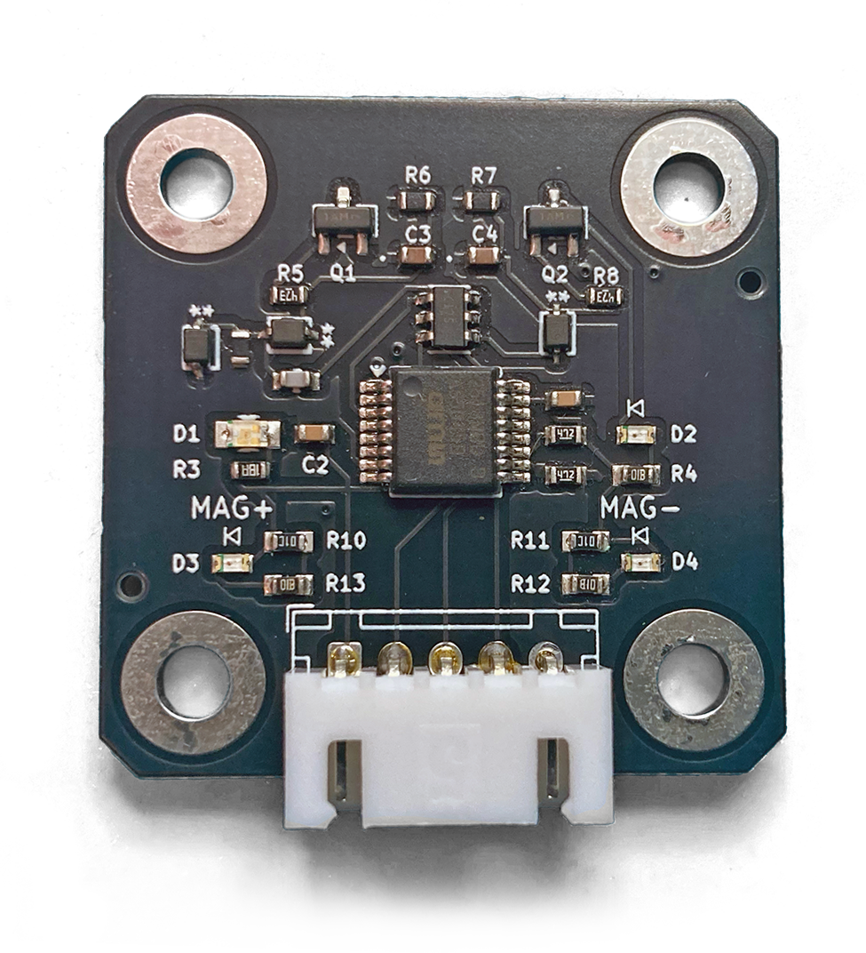
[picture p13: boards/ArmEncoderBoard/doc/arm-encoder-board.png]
arm encoder board


> Ready-made alternatives like [AS5045 Adapter Board](https://www.digikey.com/en/products/detail/ams-osram-usa-inc/as5045-adapterboard/2339623) do exist, but have extra pins not used in this project, and a footprint that makes them hard to mount.

## Power

For `3.3V` operation `VDD5V` and `VDD3V3` are bridged and routed to `VIN` (3.3V). A single `100nF` decoupling capacitor is placed at the bridge (close to the IC) to `GND`.

## Signal

The following is documented in [AS5045 specifications](./doc/AS5045Encoder.pdf):

+ Synchronous Serial Interface ([SSI](https://knowledge.ni.com/KnowledgeArticleDetails?id=kA00Z0000019MgLSAU)) with one-way communication, `MOSI` line not used
+ Compatible with SPI mode 1 (`CPOL` = `0`, `CPHA` = `1`)
+ Transfer begins when `CSn` is `LOW`
+ MSB-first, clocked data output

> The encoder continuously shifts out an 18-bit data frame containing the absolute position and flags in response to clock input without having to request this information - that's what makes its interface *SSI* instead of *SPI*.

In addition to the digital communication interface, AS5045 also exposes these pins:

+ Quadrature `A`, `B` which can take on different values (according to [grey code](https://cool-emerald.blogspot.com/2014/03/reading-rotary-encoder-using.html) specification) as the magnet angle is changing
+ Index `I`, which is signaled when the magnet passes the zero position (typically used to count complete revolutions)
+ Magnet `MagINC`, `MagDEC` pins that indicate magnetic field strength and changing of distance between sensor and magnet (can be used to troubleshoot bad readings or "wobbly" mounting where the magnet changes distance to sensor as it rotates)

## Data Format

The data frame contains 18 bits: 12 data bits, 5 status bits, and 1 parity bit.

| Bit  | Size | Name | Description
| ---- | ---- | --- | ---
| 0–11 | 12 | Position | Angle value (MSB first)
| 12 | 1 | OCF | Offset Compensation Finished
| 13 | 1 | COF | CORDIC overflow (invalid angle)
| 14 | 1 | LIN | Linearity alarm
| 15 | 1 | MagINC | Magnet too far
| 16 | 1 | MagDEC | Magnet too close
| 17 | 1 | Parity | Even parity over previous bits

In practice, it's enough to simply read the first `16` bits using [SPI.transfer16](https://docs.arduino.cc/language-reference/en/functions/communication/SPI/transfer/) function commonly available on Arduino-like microcontrollers such as Teensy.

## Indicators

LEDs are attached to quadrature and index pins as well as magnetic field status pins:

+ The `A` LED blinks when receiving quadrature input (magnet is moving)
+ The `I` LED lights when the encoder is at zero position (magnet is near zero position)
+ The `MagINC` and `MagDEC` LEDs indicate the quality of readings:

|MagINC|MagDEC|Description
|-|-|-
|`0`|`0`|Distance to magnet is not changing, magnetic field OK
|`0`|`1`|Distance to magnet is increasing
|`1`|`0`|Distance to magnet is decreasing
|`1`|`1`|Magnetic field too low (magnet too far from sensor)

The following components are used to enable this:

+ `SN74LVC2G17DBVR` two-channel Schmitt buffer
+ `BAT54WS` Schottky diodes
+ `470K` resistors (transistor base bleed)
+ `47K` resistors (transistor base resistor)
+ `100K` resistors (envelope discharge)
+ `1uF` capacitors (envelope storage)
+ `100nF` capacitor (buffer decoupling)
+ `150R` and `1K` resistors (LED current limit)
+ `MMBT3904` transistors (LED sink drivers)

The `A` quadrature signal from the encoder indicates activity and is connected in the following network:

|Signal|Pin|
|-|-|
|`A`|AS5045 `A` pin going to Schmitt buffer input
|`A_EDGE`|Cleaned edges from Schmitt buffer output
|`A_PULSE`|RC circuit that turns edges into pulses
|`A_ENV`|Envelope circuit that makes pulses last longer
|`A_BLEED`|Envelope bleed
|`A_BASE`|Transistor base input
|`BLUE_CATHODE`|Blue LED cathode
|`BLUE_ANODE`|Blue LED anode

The `I` index signal from the encoder indicates zero position and is connected in the following network:

|Signal|Pin|
|-|-|
|`I`|AS5045 `I` pin going to Schmitt buffer input
|`I_BUF`|Schmitt buffer output
|`I_ENV`|Envelope circuit that makes pulses last longer
|`I_BLEED`|Envelope bleed
|`I_BASE`|Transistor base input
|`BLUE_CATHODE`|Blue LED cathode
|`BLUE_ANODE`|Blue LED anode

### Schmitt Buffer

The Schmitt Trigger Buffer clamps quadrature signals to either `HIGH` or `LOW`, which *cleans the edges* of these signals, making them a *sharp* square wave instead of a *noisy*, approximate, square wave with *soft* edges.

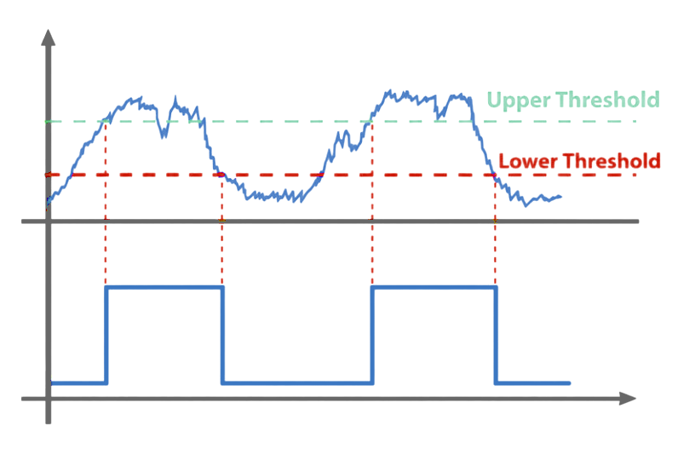
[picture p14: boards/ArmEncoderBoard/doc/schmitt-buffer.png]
schmitt buffer diagram


This conditioning is needed because the later stages (a differentiator and an integrator) amplify, and therefore are very sensitive to, noise.

### RC Filter (Differentiator)

The differentiator, implemented by using an RC (*Resistor and Capacitor*) circuit, reacts to *changes* in voltage level.

If the input voltage changes from `HIGH` to `LOW`, the output from the differentiator is `HIGH`, same from `LOW` back to `HIGH`. The differentiator stays `LOW` when the voltage is not changing.

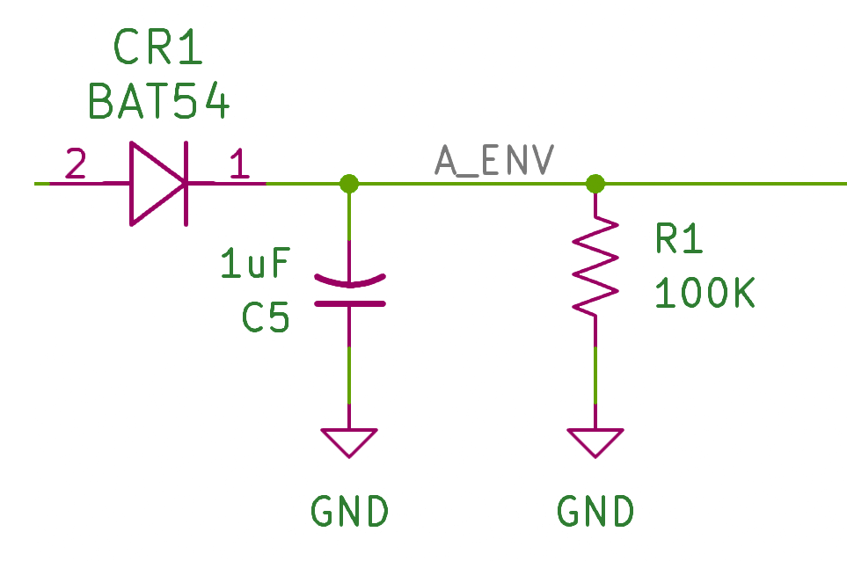
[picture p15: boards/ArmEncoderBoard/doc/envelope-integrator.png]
rc integrator


This makes the `A` LED light only when the quadrature signal changes. It's the only way to make an *activity* LED for this kind of signal because a quadrature channel may be left either `HIGH` or `LOW` depending on when the thing being measured stops moving (there is a truth table called the [grey code](https://cool-emerald.blogspot.com/2014/03/reading-rotary-encoder-using.html) that describes the possible states).

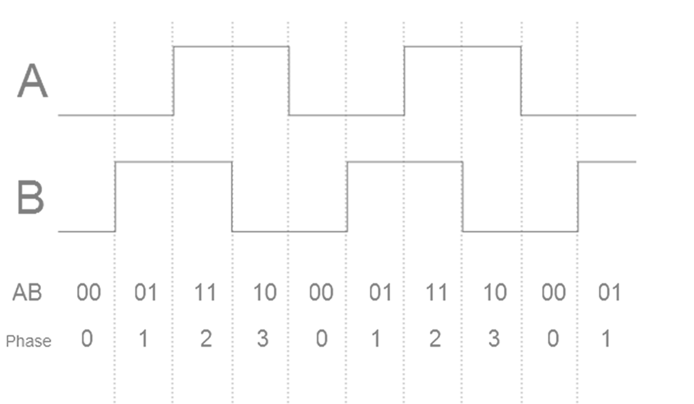
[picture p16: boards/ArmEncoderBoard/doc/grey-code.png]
grey code


### Envelope Generator (Integrator)

Envelope generators modify the transient characteristics of the incoming signal. The one used here acts like an integrator (it accumulates a value over time) by making the signal rise quickly (fast attack) but decay slowly (slow release).

> Fast attack/slow release combination creates "sustain" which enables the LED indicators to stay on long enough to be seen as a "blink" by the human eye after the differentiator detects a change (movement).

envelope generator

Without this part of the circuit, the LEDs would strobe so fast that to a human they would look dimly lit.

### Transistors

Transistors are used to drive LEDs from the power source, using AS5045's A/I pins as on/off switches so they don't drive LEDs directly.

+ Emitter connects to `GND`
+ Collector connects to LED cathode
+ Base connects to `ENV` through `47K` base resistor
+ Base connects to `GND` through `470K` pull-down resistor
+ LED anode connects to `3.3V` through LED resistor (depending on LED color)

### Open-Drain Outputs

The `MagINC` and `MagDEC` pins on AS5045 are open-drain, active-low outputs:

+ When the signals are off (`High-Z`), `10K` resistors are used to pull the lines up to `VIN` bus voltage, making the voltage potential across the corresponding LEDs zero and turning them off (both cathode and anode are bridged to `VIN`).
+ When the signals are on (`LOW`), the LED cathodes get bridged to `GND` through these AS5045 pins (and `1K` current-limiting resistors), while LED anodes remain bridged to `VIN` as before, generating a positive voltage potential and turning the LEDs on.

## Connector

The `JST-XH` connector is designed to accomodate a 5-pin `SSI` interface:

|Position|1|2|3|4|5
|-|-|-|-|-|-|
|Signal|`3V3`|`CS`|`SCK`|`MISO`|`GND`|

This is designed for a simple 5-terminal ribbon with a JST-XH locking connector crimped on.

## Miscellaneous

The following components appear on the board other than the encoder and the connector:

+ `100nF` (`0.1uF`) to `GND` on `VDD`: decoupling capacitor
+ `VDD` and `VDD3V3` bridged on `VIN`: for 3.3V operation
+ `4.7K` to `GND` on `SCK`: clock pull-down
+ `4.7K` to `VIN` on `CS`: chip select pull-up

## Example

```c++
#define CS              10
#define MAG_INC_MASK    0x0001
#define LIN_MASK        0x0002
#define COF_MASK        0x0004
#define OCF_MASK        0x0008
#define POSITION_MASK   0xFFF0
#define POSITION_SHIFT  4

SPISettings spiSettings(
  1e6,
  MSBFIRST,
  SPI_MODE0
);

void setup()
{
  SPI.begin();

  pinMode(CS, OUTPUT);
  digitalWrite(CS, HIGH);
}

void loop()
{
  // Select
  digitalWrite(CS, LOW);

  // Read
  SPI.beginTransaction(spiSettings);
  uint16_t data = SPI.transfer16(0);
  SPI.endTransaction();

  // Deselect
  digitalWrite(CS, HIGH);

  // Position
  uint16_t position = (data & POSITION_MASK) >> POSITION_SHIFT;

  // Offset Compensation Finished (OCF)
  bool ocf = data & OCF_MASK;

  // CORDIC Overflow (COF)
  bool cof = data & COF_MASK;

  // Linearity Alarm (LIN)
  bool lin = data & LIN_MASK;

  // Magnetic field too low (MAGINC)
  bool magInc = data & MAG_INC_MASK;

  // Derive "is the reading valid?" from flags
  bool valid = ocf && !cof;

  // Derive "is the reading high quality?" from flags
  bool quality = !lin && !magInc;
}
```

## Bill of Materials

|Component|Description|
|-|-|
|[AS5045B-ASST SSOP16 LF T&RDP](https://www.digikey.com/en/products/detail/ams-osram-usa-inc/as5045b-asst-ssop16-lf-t-rdp/4896030)|Hall Effect Encoder|
|[CC0603KRX7R9BB104](https://www.digikey.com/en/products/detail/yageo/cc0603krx7r9bb104/2103082)|`100nF` Decoupling Capacitor|
|[CC0603JRX7R7BB105](https://www.digikey.com/en/products/detail/yageo/cc0603jrx7r7bb105/7164369)|`1uF` Envelope Capacitor|
|[RCG06031K00FKEA](https://www.digikey.com/en/products/detail/vishay-dale/rcg06031k00fkea/4172389)|`1K` Red LED Resistor|
|[CR0603-FX-4701ELF](https://www.digikey.com/en/products/detail/bourns-inc/cr0603-fx-4701elf/3740916)|`4.7K` Pull-Down/Pull-Up Resistor|
|[RC0603FR-0747KL](https://www.digikey.com/en/products/detail/yageo/rc0603fr-0747kl/727253)|`47K` Transistor Base Resistor|
|[CRCW0603100KFKEA](https://www.digikey.com/en/products/detail/vishay-dale/crcw0603100kfkea/1174896)|`100K` Envelope Pull-Down Resistor|
|[RC0603FR-07150RL](https://www.digikey.com/en/products/detail/yageo/rc0603fr-07150rl/726958)|`150R` Blue LED Resistor|
|[RC0603FR-07470KL](https://www.digikey.com/en/products/detail/yageo/rc0603fr-07470kl/727257)|`470K` Envelope Bleed Resistor|
|[CRCW060310K0FKEA](https://www.digikey.com/en/products/detail/vishay-dale/crcw060310k0fkea/1174782)|`10K` Open-Drain Pull-Up Resistors|
|[SN74LVC2G17DBVR](https://www.digikey.com/en/products/detail/umw/sn74lvc2g17dbvr/24890103)|Schmitt Buffer (2-channel)|
|[MMBT3904LT1G](https://www.digikey.com/en/products/detail/onsemi/MMBT3904LT1G/919601)|Transistor|
|[BAT54WS-7-F](https://www.digikey.com/en/products/detail/diodes-incorporated/bat54ws-7-f/804865)|Envelope Diode|
|[NCD0603R1](https://www.lcsc.com/product-detail/C84263.html?s_z=n_NCD0603R1)|Red LED `0603`|
|[150080BS75000](https://www.digikey.com/en/products/detail/w%C3%BCrth-elektronik/150080bs75000/4489912)|Blue LED `0805`|
|[B5B-XH-A](https://www.digikey.com/en/products/detail/jst-sales-america-inc/b5b-xh-a/1530483)|5-pin `JST-XH` connector (2.5mm pitch)|

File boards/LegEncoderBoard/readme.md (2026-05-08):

# Leg Encoder Board

A custom board that simplifies mounting `AS5047P` hall-effect on-axis encoder with 14-bit resolution on robot wheel hubs.

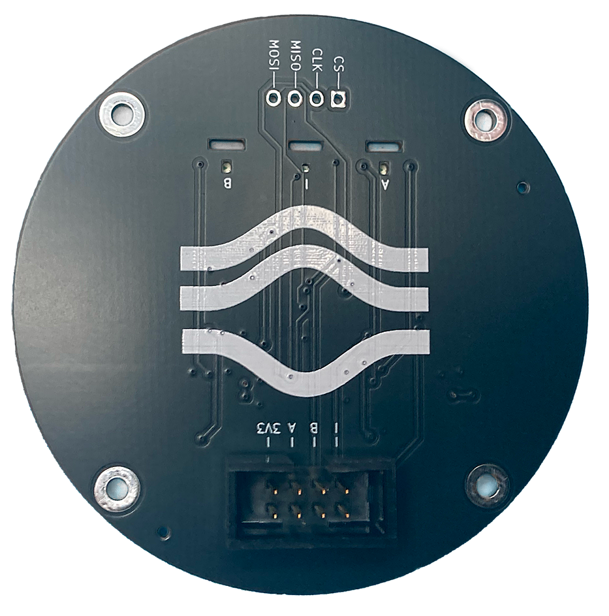
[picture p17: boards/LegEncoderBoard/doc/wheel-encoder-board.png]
wheel encoder board


> Ready-made alternatives like [SideView Tech](https://www.amazon.com/AS5047P-Magnetic-Position-Breakout-Compatible/dp/B0DLJ6XDNM) and [AS5047P Adapter Board](https://www.digikey.com/en/products/detail/ams-osram-usa-inc/as5047p-adapterboard/5452344) do exist, but have extra pins not used in this project and a board shape that makes them hard to mount.

## Power

For `3.3V` operation `VDD` and `VDD3V3` are bridged and decoupled to `GND` via `100nF` decoupling capacitor and `10uF` bypass capacitor.

Another `1uF` bulk capacitor is on `VDD3V3` line for additional stabilization.

## Signal

The [AS5047P documentation](./doc/AS5047P.pdf) specifies that `A` and `B` pins output a quadrature signal, and an additional `I` pin outputs index (one pulse per complete revolution). In practice, the index is `HIGH` whenever the encoder is approximately near its zero position.

## Indicators

LEDs are attached to quadrature and index (`A`, `B`, `I`) encoder outputs:
+ The `A` and `B` quadrature LEDs blink when the angle changes
+ The `I` index LED lights when the encoder is approximately over its zero position

The following components are used to enable this:

+ `SN74LVC3G17DCTRE4` triple Schmitt buffer
+ `BAT54WS` Schottky diodes
+ `470K` resistors (transistor base bleed)
+ `47K` resistors (transistor base resistor)
+ `100K` resistors (envelope discharge)
+ `1uF` capacitors (envelope storage)
+ `100nF` capacitor (buffer decoupling)
+ `10nF` capacitor (RC storage)
+ `MMBT3904` transistors (LED sink drivers)

Quadrature signals (`A` and `B`) are connected in the following network:

|Signal|Pin|
|-|-|
|`A`, `B`|AS5047 A, B pins going to Schmitt buffer inputs
|`A_BUF`, `B_BUF`|Schmitt buffer output
|`A_EDGE`, `B_EDGE`|Cleaned edges from Schmitt buffer output
|`A_PULSE`, `B_PULSE`|RC circuit that turns edges into pulses
|`A_ENV`, `B_ENV`|Envelope circuit that makes pulses last longer
|`A_BASE`, `B_BASE`|Transistor base
|`A_LED_CATHODE`, `B_LED_CATHODE`|LED cathode
|`A_LED_ANODE`, `B_LED_ANODE`|LED anode

Index signal (`I`) is connected in the following network:

|Signal|Pin|
|-|-|
|`I`|AS5047 I pin to Schmitt buffer input
|`I_BUF`|Schmitt buffer output
|`I_ENV`|Envelope circuit that makes pulses last longer
|`I_BASE`|Transistor base
|`I_LED_CATHODE`|LED cathode
|`I_LED_ANODE`|LED anode

Both Quadrature and Index signals use an integrator circuit to make fast changes visible. Quadrature signals add a differentiator before the integrator to make the lights react only to changes in the quadrature signal, rather than the actual signal.

### Schmitt Buffer

The Schmitt Trigger Buffer clamps quadrature signals to either `HIGH` or `LOW`, which *cleans the edges* of these signals, making them a *sharp* square wave instead of a *noisy*, approximate, square wave with *soft* edges.

schmitt buffer diagram

This conditioning is needed because the later stages (a differentiator and an integrator) amplify, and therefore are very sensitive to, noise.

### RC Filter (Differentiator)

The differentiator, implemented by using an RC (*Resistor and Capacitor*) circuit, reacts to *changes* in voltage level.

If the input voltage changes from `HIGH` to `LOW`, the output from the differentiator is `HIGH`, same from `LOW` back to `HIGH`. The differentiator stays `LOW` when the voltage is not changing.

rc integrator

This makes the LEDs light only when the quadrature signal changes. It's the only way to make an *activity* LED for this kind of signal because quadrature `A` and `B` channels may be left either `HIGH` or `LOW` depending on when the thing being measured stops moving (there is a truth table called the [grey code](https://cool-emerald.blogspot.com/2014/03/reading-rotary-encoder-using.html) that describes the possible states).

grey code

### Envelope Generator (Integrator)

Envelope generators modify the transient characteristics of the incoming signal. The one used here acts like an integrator (it accumulates a value over time) by making the signal rise quickly (fast attack) but decay slowly (slow release).

> Fast attack/slow release combination creates "sustain" which enables the LED indicators to stay on long enough to be seen as a "blink" by the human eye after the differentiator detects a change (movement).

envelope generator

Without this part of the circuit, the LEDs would strobe so fast that to a human they would look dimly lit.

### Transistors

Transistors are used to drive LEDs from the power source, using AS5047's A/B/I pins as on/off switches so they don't drive LEDs directly.

+ Emitter connects to `GND`
+ Collector connects to `LED_CATHODE`
+ Base connects to `ENV` through `47K` base resistor (transitor base is a diode much like an LED, and needs a current-limiting resistor, otherwise Teensy will dump all its available current into the gate, which adds up quickly)
+ Base connects to `GND` through `470K` pull-down resistor (this helps ensure the gate stays closed when connected to nothing, such as during boot)

### Indicators

+ LED anode (`LED_CATHODE`) connects to `3.3V` through LED resistor (depending on LED color)
+ LED cathode (`LED_ANODE`) connects to transistor collector

## Connector

The board uses an IDC connector with 2 rows of 4 pins. This enables twisting each of the four signal wires with ground for better interference rejection.

Conveniently, [CAT5E](https://www.amazon.com/dp/B00KWS6TWS) cables have this precise layout: 8 wires, 4 of them signals, 4 of them grounds, each signal twisted with its ground along the entire length of the cable.

All that remains is cutting off the `RJ45` connectors and crimping on [Molex 0022552082](https://www.digikey.com/en/products/detail/molex/0022552082/313629) / [Molex 0016020086](https://www.digikey.com/en/products/detail/molex/0016020086/467788) to make female locking connectors that fit into IDC male receptacles.

|Column|1|2|3|4|
|-|-|-|-|-|
|Row 1|`3V3`|`GND`|`A`|`GND`|
|Row 2|`B`|`GND`|`I`|`GND`|

## Example

The following can be used to initialize the encoder on [Teensy 4.0](https://www.sparkfun.com/teensy-4-0.html) and read quadrature input:

```c++
#include <Arduino.h>
#include <Encoder.h>

#define PIN_A 2
#define PIN_B 3
#define PIN_I 4

Encoder encoder(PIN_A, PIN_B);
volatile uint32_t revolutions = 0;

void indexInterrupt()
{
  revolutions++;
}

void setup()
{
  Serial.begin(115200);
  while (!Serial && millis() < 2000);

  pinMode(PIN_A, INPUT);
  pinMode(PIN_B, INPUT);
  pinMode(PIN_I, INPUT);

  attachInterrupt(
    digitalPinToInterrupt(PIN_I),
    indexInterrupt,
    RISING
  );

  encoder.write(0);
}

void loop()
{
  int32_t counts = encoder.read();

  Serial.print("counts ");
  Serial.print(counts);
  Serial.print("revolutions ");
  Serial.println(revolutions);

  delay(10);
}
```

## Bill of Materials

|Component|Description|
|-|-|
|[AS5047P-ATST](https://www.digikey.com/en/products/detail/ams-osram-usa-inc/as5047p-atst-tssop14-lf-t-rdp/5288535)|Encoder|
|[CC0603KRX7R9BB104](https://www.digikey.com/en/products/detail/yageo/cc0603krx7r9bb104/2103082)|`100nF` Decoupling Capacitor|
|[GRM1885C1H103JA01D](https://www.digikey.com/en/models/4421555)|`10nF` Bypass Capacitor|
|[CC0603JRX7R7BB105](https://www.digikey.com/en/products/detail/yageo/CC0603JRX7R7BB105/7164369)|`1uF` Bulk Capacitor, Envelope Capacitor|
|[150080BS75000](https://www.digikey.com/en/products/detail/w%C3%BCrth-elektronik/)|Blue LED for A and B channels|
|[NCD0603R1](https://www.lcsc.com/product-detail/C84263.html?s_z=s_C84263)|Red LED for I channel|
|[RC0603FR-07470KL](https://www.digikey.com/en/products/detail/yageo/rc0603fr-07470kl/727257)|`470K` Bleed Resistor|
|[RCG06031K00FKEA](https://www.digikey.com/en/products/detail/vishay-dale/rcg06031k00fkea/4172389)|`1K` Resistor (Red LED)|
|[RC0603FR-0747KL](https://www.digikey.com/en/products/detail/yageo/RC0603FR-0747KL/730200)|`47K` Transistor Base Resistor|
|[CRCW0603100KFKEA](https://www.digikey.com/en/products/detail/vishay-dale/crcw0603100kfkea/1174896)|`100K` Discharge Resistor|
|[RC0603FR-07150RL](https://www.digikey.com/en/products/detail/yageo/rc0603fr-07150rl/726958)|`150 Ohm` Resistor (Blue LED)|
|[RC0603FR-0722RL](https://www.digikey.com/en/products/detail/yageo/rc0603fr-0722rl/727055)|`22 Ohm` Series Resistor (A/B/I outputs to connector)|
|[SN74LVC3G17DCTRE4](https://www.digikey.com/en/products/detail/texas-instruments/sn74lvc3g17dctre4/1592395)|Schmitt-trigger buffer|
|[BAT54WS-7-F](https://www.digikey.com/en/products/detail/diodes-incorporated/BAT54WS-7-F/804865)|Envelope Diode|
|[MMBT3904LT1G](https://www.digikey.com/en/products/detail/onsemi/MMBT3904LT1G/919601)|LED Transistor|

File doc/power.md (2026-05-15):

# Power System

## Overview

The robot runs from the battery, charging if plugged in. A circuit breaker or an E-Stop can be used to turn off the robot while the battery is charging.

Power System Schematic

## AC

The AC part of the circuit includes an energy meter and a green pilot light.

## DC

The DC part of the circuit includes the battery, breaker, contactor wired to an emergency stop, and a red pilot light.

The `24V` bus after the main breaker includes voltage and current sensing: analog front panel voltmeter/ammeter and digital meters on the main robot board that calculate and advertise the battery charge and power usage.

Most of the actuators and motors are on the `12V` bus, but the large torso servo needs at least `24V` to operate.

## Components

|Component|Description|
|-|-|
|[Moseworth LiFePO4](https://www.amazon.com/dp/B0FX8HR52D)|`24V` `60Ah` Lithium Battery|
|[LiTime Charger](https://www.amazon.com/dp/B0BLRR73GD)|`24V` `20A` LiFePO4 Battery Charger|
|[D52-2066](https://www.amazon.com/dp/B094F98PYF)|AC Bus `110V` `100A` Energy Meter|
|[Baomain AC Analog Voltmeter](https://www.amazon.com/dp/B07S376BV3)|AC Bus `0-150V` Voltage Meter|
|[Green AC Pilot Light](https://www.amazon.com/dp/B0CSZ6S7LH)|AC Bus `110V` Supply Light|
|[E-Stop](https://www.amazon.com/dp/B079FKJG26)|DC Bus Emergency Stop/Reset|
|[TXBD1-100](https://www.amazon.com/dp/B0C53PMC7D)|DC Bus Circuit Breaker `2P` `100A`|
|[Contactor](https://www.amazon.com/dp/B0F6BZVVFX)|DC Bus `1000V` `150A` Contactor|
|[Inline Fuse](https://www.amazon.com/dp/B0C15H3F9M)|DC `5A` Inline Fuse for Contactor Coil|
|[Daygreen A2D12C100](https://daygreen.com/products/24v-to-12v-100a-1200w-dc-dc-step-down-converter-voltage-regulator-3-year-warranty)|`24V` to `12V` `100A` `1200W` DC-DC Step Down Converter|
|[Baomain DC Analog Voltmeter](https://www.amazon.com/dp/B01KDVU1N6)|DC Bus `0-30V` Voltage Meter|
|[Baomain DC Analog Ammeter](https://www.amazon.com/dp/B01FAVYELY)|DC Bus `0-100A` Current Meter|
|[Red DC Pilot Light](https://www.amazon.com/dp/B0CC4R2VR7)|DC Bus `24V` Supply Light|

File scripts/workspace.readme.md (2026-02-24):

# Calculate Robot Arm Workspace

A Python script that computes the reachable workspace of a robot arm from a URDF model.

It generates:

* A **convex hull** of the reachable tip positions
* A **non-convex volumetric mesh** using voxelization + marching cubes

Designed for:

* Ubuntu 20.04
* ROS Noetic
* Python 3

---

## Dependencies

ROS packages (usually already available in Noetic):

* `urdf_parser_py`
* `kdl_parser_py`
* `PyKDL`

Python packages:

```bash
pip3 install numpy scipy trimesh scikit-image
```

---

## How It Works

1. Loads URDF
2. Builds KDL kinematic chain
3. Extracts joint limits
4. Randomly samples joint space
5. Computes forward kinematics
6. Builds:

   * Convex hull mesh
   * Non-convex volume mesh

---

## Usage

```bash
python3 workspace.py \
  --urdf /description/robot.urdf \
  --base base_link \
  --tip tip_link \
  --samples 300000 \
  --seed 0 \
  --voxel_size 0.01 \
  --closing_iters 2 \
  --min_component_volume 0 \
  --hull_out workspace-hull.stl \
  --mesh_out workspace-mesh.stl
```

---

## Parameters

| Parameter | Description |
| --- | --- |
| `--urdf` | Path to URDF file |
| `--base` | Base link name |
| `--tip` | End-effector (tip) link name |
| `--samples` | Number of random joint samples |
| `--seed` | RNG seed for reproducibility |
| `--voxel_size` | Voxel resolution in meters (recommended: 0.005–0.02) |
| `--closing_iters` | Morphological closing iterations (fills gaps from sparse sampling) |
| `--min_component_volume` | Remove mesh components smaller than this volume (m³) |
| `--hull_out` | Output STL path for convex hull |
| `--mesh_out` | Output STL path for non-convex volume mesh |

---

## Recommended Settings

For a ~1 meter reach arm:

| Quality | Samples | Voxel Size |
| --- | --- | --- |
| Fast preview  | 50k | 0.02 |
| Balanced | 200k | 0.01 |
| High fidelity | 400k+ | 0.005 |

⚠ Very small voxel sizes can require large amounts of RAM.

---

## Output Files

* `workspace-hull.stl` — convex hull (fast, bounding volume)
* `workspace-mesh.stl` — non-convex volumetric workspace

Both can be imported into CAD tools like:

* SolidWorks
* Fusion 360
* Blender
* FreeCAD

---

## Notes

* This computes **geometric reachability only**.
* It does not account for:

  * Self-collisions
  * Environment collisions
  * Joint torque limits
  * Dynamic constraints

It represents purely kinematic reachable space.

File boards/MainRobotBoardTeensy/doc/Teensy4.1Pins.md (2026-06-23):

|Pin|Functions
|-|-|
|0|PWM CRX2 CS1 RX1
|1|PWM CTX2 MISO1 TX1
|2|PWM OUT2
|3|PWM LRCLK2
|4|PWM BLK2
|5|PWM IN2
|6|PWM OUT1D
|7|PWM OUT1A RX2
|8|PWM IN1 TX2
|9|PWM OUT1C
|10|PWM MQSR CS
|11|PWM CTX1 MOSI
|12|PWM MQSL MISO
|13|PWM SCK
|14|PWM SPDIFOUT TX3 A0
|15|PWM SPDIFIN RX3 A1
|16|SCL1 RX4 A2
|17|SDA1 TX4 A3
|18|PWM SDA A4
|19|PWM SCL A5
|20|LRCLK1 TX5 A6
|21|BCLK1 RX5 A7
|22|PWM CTX1 A8
|23|PWM MCLK1 CRX1 A9
|24|PWM SCL2 TX6 A10
|25|PWM SDA2 RX6 A11
|26|MOSI1 A12
|27|SCK1 A13
|28|PWM RX7
|29|PWM TX7
|30|CRX3
|31|CTX3
|32|OUT1B
|33|PWM MCLK2
|34|RX8
|35|TX8
|36|PWM CS
|37|PWM CS
|38|IN1 CS1 A14
|39|OUT1A MISO1 A15
|40|A16
|41|A17

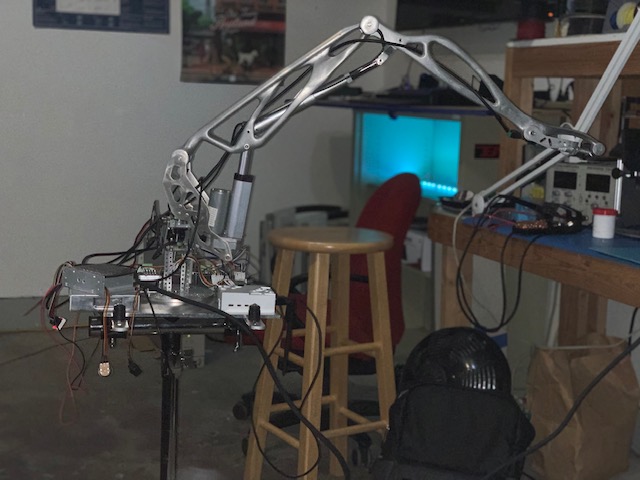
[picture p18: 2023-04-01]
design/extended.jpg

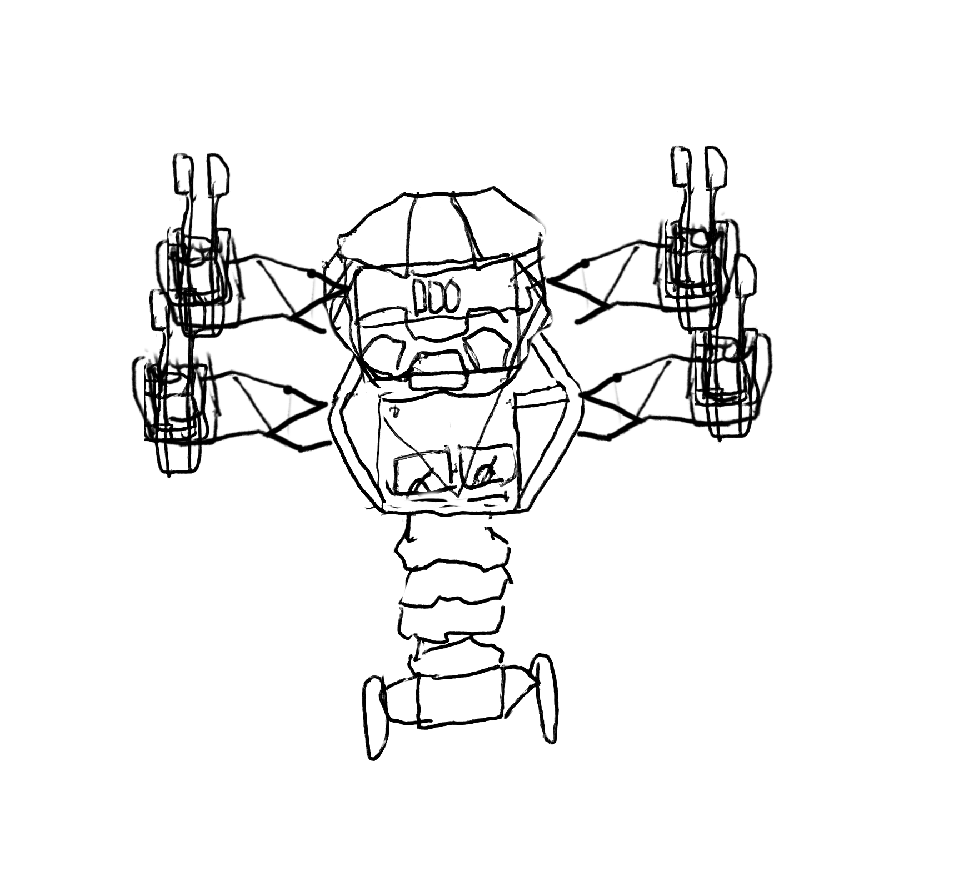
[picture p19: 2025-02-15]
design/front-export.png

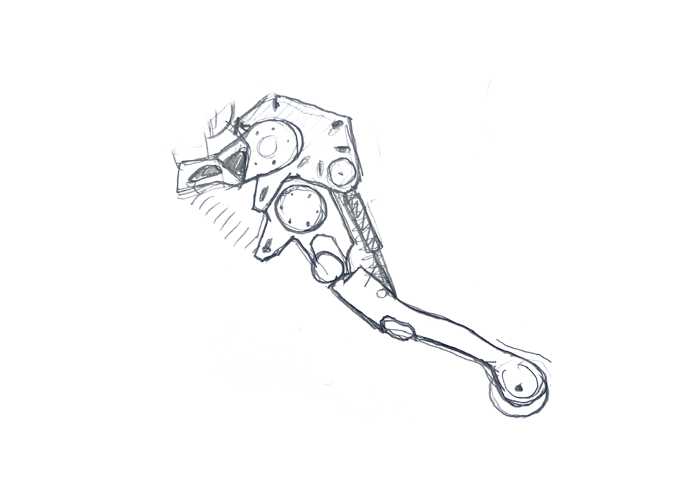
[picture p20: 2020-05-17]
design/leg.png

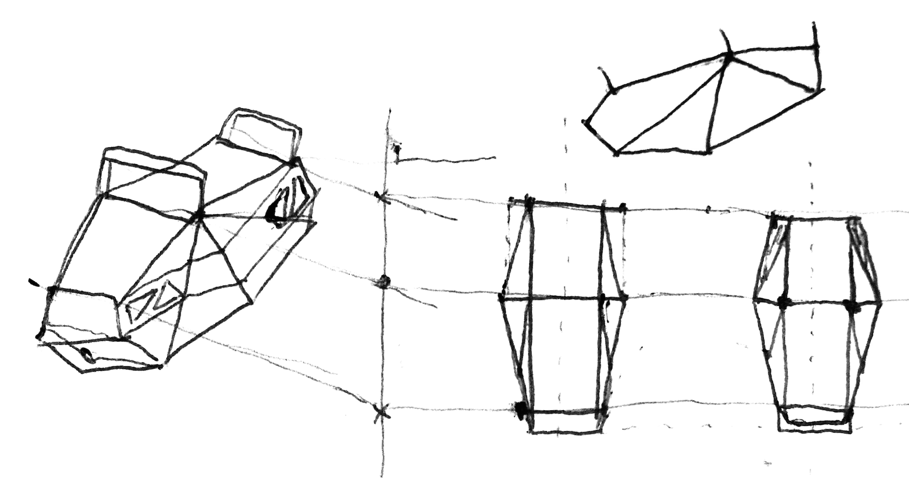
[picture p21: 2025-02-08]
design/chest-redesign.png

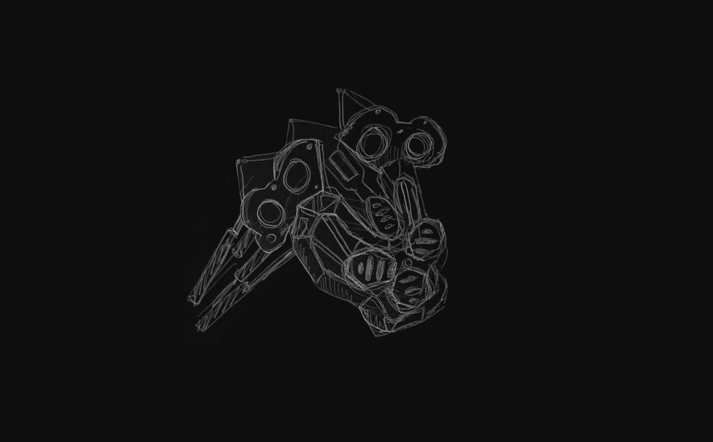
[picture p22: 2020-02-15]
design/robot-face.jpg

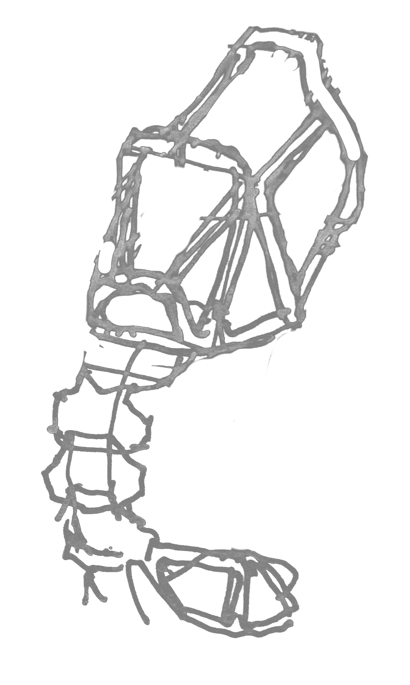
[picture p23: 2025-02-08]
design/chest-redesign3.png

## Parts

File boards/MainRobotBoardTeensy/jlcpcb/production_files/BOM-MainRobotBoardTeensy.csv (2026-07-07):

Comment | Designator | Footprint | LCSC | Quantity
100K | R59,R61,R75,R77,R79,R81,R83,R85,R87,R89,R91,R93,R95,R97 | CRCW0603100KFKEA | C844916 | 14
100nF | C9 | CC0603KRX7R9BB104 | C14663 | 1
10K | R2,R38,R39,R40,R41,R42,R43,R44,R45,R46,R47,R48,R49,R50,R51,R52,R53,R58,R60,R62,R64,R66,R68,R74,R76,R78,R80,R82,R84,R86,R88,R90,R92,R94,R96 | CRCW060310K0FKEA | C844918 | 35
10nF | C10,C2 | C0402C103J4RACTU | C152817 | 2
150R | R11,R12,R13,R14,R15,R16,R17,R18,R19,R20,R21,R22 | RESC1607X60N | C114608 | 12
1K | R65 | RCG06031K00FKEA | C4264491 | 1
1uF | C1 | CC0603JRX7R7BB105 | C519560 | 1
2.2K | R34,R35,R36 | RC0603FR-072K2L | C114662 | 3
22K | R63 | 0603WAF2202T5E | C31850 | 1
360K | R1 | RC0603FR-07360KL | C137740 | 1
470R | R100,R101,R102,R103,R104,R105,R106,R107,R3,R4,R5,R6,R7,R8,R98,R99 | RC0603FR-07470RL | C114669 | 16
47R | R23,R24,R25,R26,R27,R28,R29,R30,R31,R32,R33 | RESC1608X55 | C114623 | 11
47nF | C3,C4,C5 | CAPC1608X90N | C1622 | 3
AO3400A | Q1,Q10,Q11,Q12,Q13,Q14,Q15,Q16,Q17,Q18,Q19,Q2,Q20,Q3,Q4,Q5,Q6,Q9 | AO3400A | C20917 | 18
BLUELED | D10,D11,D12,D13,D14,D15,D16,D17,D18,D19,D20,D9 | 150080BS75000_Modified | C6067133 | 12
REDLED | D1,D2,D3,D4,D5,D6 | XL-1608SURC-06 | C965799 | 6
SN74HC08DR | U3,U4,U6 | SN74HC08DR | C337768 | 3
TLC555CDR | U2 | TLC555CDR | C6986 | 1
74HCT125D | U9 | 74HCT125D |  | 1
Teensy4.1 | U1 | Teensy41 |  | 1
74HCT125D | U5 | 74HCT125D |  | 1
Screw_Terminal_01x02 | J4 | TerminalBlock_Phoenix_MKDS-1,5-2-5.08_1x02_P5.08mm_Horizontal |  | 1

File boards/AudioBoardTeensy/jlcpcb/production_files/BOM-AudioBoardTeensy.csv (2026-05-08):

Comment | Designator | Footprint | LCSC | Quantity
100K | R3,R4 | CRCW0603100KFKEA | C2907088 | 2
10uF | C1 | CL10A106KP8NNNC | C19702 | 1
1K | R1 | RCG06031K00FKEA | C21190 | 1
2K | R2 | 0603WAF2001T5E | C22975 | 1

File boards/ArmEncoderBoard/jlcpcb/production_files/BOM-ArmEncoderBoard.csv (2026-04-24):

Comment | Designator | Footprint | LCSC | Quantity
100K | R6,R7,R9 | CRCW0603100KFKEA | C844916 | 3
100nF | C1,C2 | CC0603KRX7R9BB104 | C14663 | 2
10K | R10,R11 | CRCW060310K0FKEA | C95204 | 2
10nF | C5 | GRM1885C1H103JA01D | C85973 | 1
150R | R3 | RESC1607X60N | C114608 | 1
1K | R12,R13,R4 | RCG06031K00FKEA | C4264491 | 3
1uF | C3,C4 | CC0603JRX7R7BB105-L | C519560 | 2
4.7K | R1,R2 | CR0603-FX-4701ELF | C840629 | 2
47K | R5,R8 | RC0603FR-0747KL | C105579 | 2
AS5045B | U2 | SSOP-16_5.3x6.2mm_P0.65mm | C5375289 | 1
BAT54 | CR1,CR2,CR3 | BAT54WS-7-F | C124205 | 3
LEDBLUE | D1 | 150080BS75000_Modified | C6067133 | 1
LEDRED | D2,D3,D4 | NCD0603R1 | C84263 | 3
SN74LVC2G17DBVR | U1 | SN74LVC2G17DBVR | C10429 | 1
SS8050 | Q1,Q2 | SOT-23 | C81464 | 2

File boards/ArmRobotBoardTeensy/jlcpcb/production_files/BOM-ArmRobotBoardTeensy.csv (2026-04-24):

Comment | Designator | Footprint | LCSC | Quantity
0.01uF | C2 | C0402C103J4RACTU | C2167451 | 1
100K | R14,R17,R9 | CRCW0603100KFKEA | C844916 | 3
10K | R15,R8 | CRCW060310K0FKEA | C844918 | 2
150R | R1,R11,R2,R3,R4,R6,R7 | RCG06031K00FKEA | C114608 | 7
1K | R10,R12,R13,R5 | RCG06031K00FKEA | C4264491 | 4
1uF | C1 | CC0603JRX7R7BB105 | C519560 | 1
360K | R16 | RC0603FR-07360KL | C137740 | 1
5.1K | R18,R19,R20 | RC0603FR-075K1L | C105580 | 3
BLUE LED | D1,D2,D3,D4,D6,D7,D9 | 150080BS75000_Modified | C6067133 | 7
RED LED | D10,D11,D5,D8 | NCD0603R1 | C84263 | 4
SMMBT3904LT1G | Q1 | SMMBT3904LT1G | C84555 | 1
SN74HC08DR | U3,U4 | SN74HC08DR | C337768 | 2
TLC555CDR | U2 | TLC555CDR | C6986 | 1

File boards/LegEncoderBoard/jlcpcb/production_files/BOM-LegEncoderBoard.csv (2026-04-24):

Comment | Designator | Footprint | LCSC | Quantity
100K | R1,R10,R16,R17,R5 | CRCW0603100KFKEA | C844916 | 5
100nF | C1,C4 | CC0603KRX7R9BB104 | C14663 | 2
10nF | C2,C8,C9 | GRM1885C1H103JA01D | C85973 | 3
150R | R6,R9 | RESC1607X60N | C114608 | 2
1K | R4 | RCG06031K00FKEA | C4264491 | 1
1uF | C3,C5,C6,C7 | CC0603JRX7R7BB105 | C519560 | 4
22R | R13,R14,R15 | RC0603FR-0722RL | C107701 | 3
470K | R12,R3,R8 | RC0603FR-07470KL | C114622 | 3
47K | R11,R2,R7 | RC0603FR-0747KL | C105579 | 3
AS5047P-ATST | U1 | AS5047P-ASST | C962063 | 1
BAT54 | CR1,CR2,CR3,CR4,CR5 | BAT54WS-7-F | C124205 | 5
BLUELED | D2,D3 | 150080BS75000_Modified | C6067133 | 2
MMBT3904 | Q1,Q2,Q3 | MMBT3904LT1G | C81464 | 3
REDLED | D1 | NCD0603R1 | C84263 | 1
SN74LVC3G17DCTR | U2 | SN74LVC3G17DCTR | C18213 | 1

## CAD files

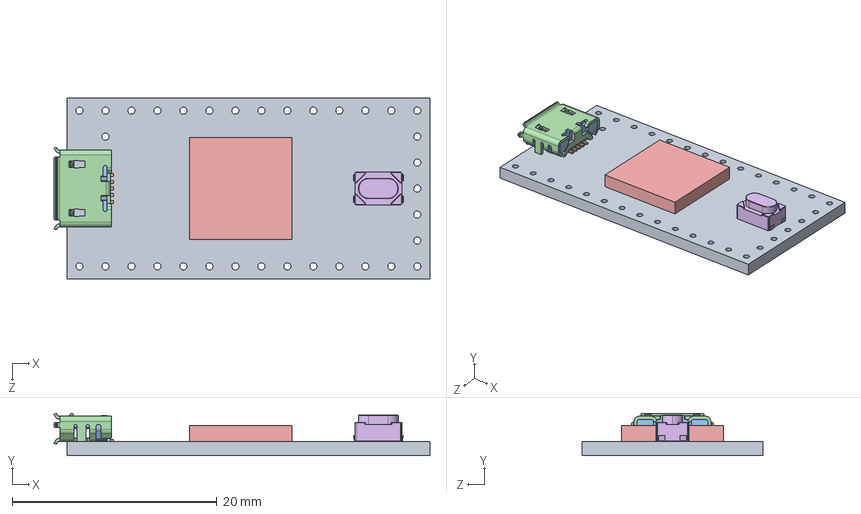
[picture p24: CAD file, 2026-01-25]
boards/AudioBoardTeensy/Dependencies/Teensy/Teensy_4.0_Assembly.STEP
36.8 x 4.12 x 17.7 mm
Teensy_4.0_PCB
Micro USB-B Female 5Pin SMD
NXP iMXRT1062
SKRPACE010 v4

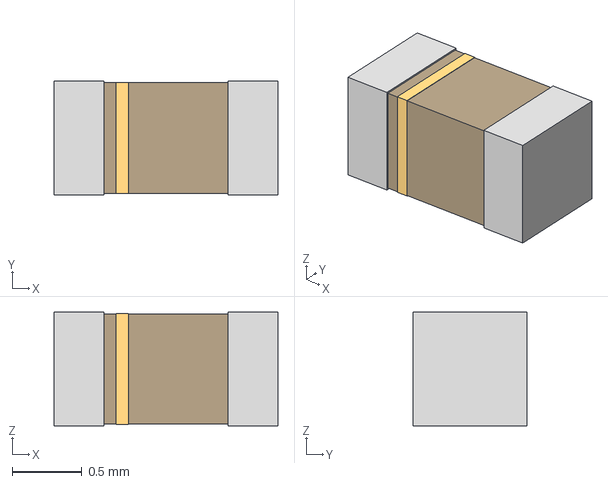
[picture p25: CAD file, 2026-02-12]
boards/ArmEncoderBoard/dependencies/Capacitor10nF/GRM1885C1H103JA01D.step
1.60 x 0.812 x 0.813 mm

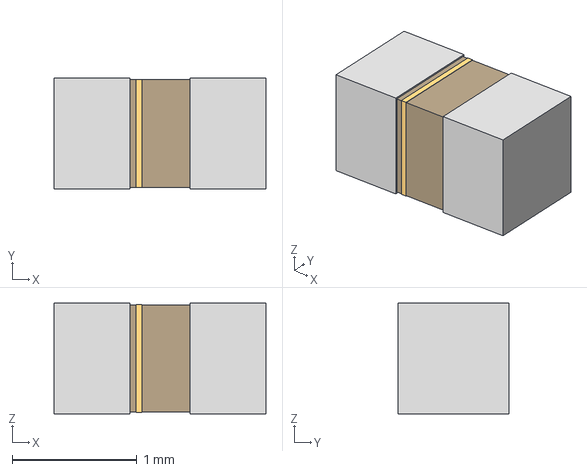
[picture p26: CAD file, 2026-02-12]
boards/ArmEncoderBoard/dependencies/Capacitor1uF/CC0603JRX7R7BB105.step
1.70 x 0.888 x 0.889 mm

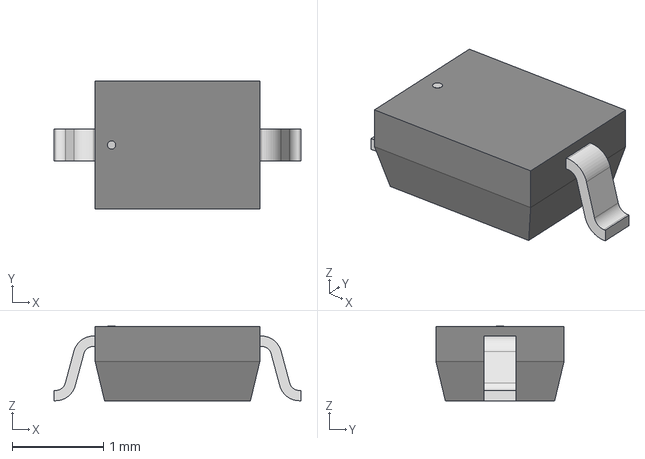
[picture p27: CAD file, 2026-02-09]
boards/ArmEncoderBoard/dependencies/EnvelopeDiode/BAT54WS-7-F.step
2.70 x 1.40 x 0.815 mm

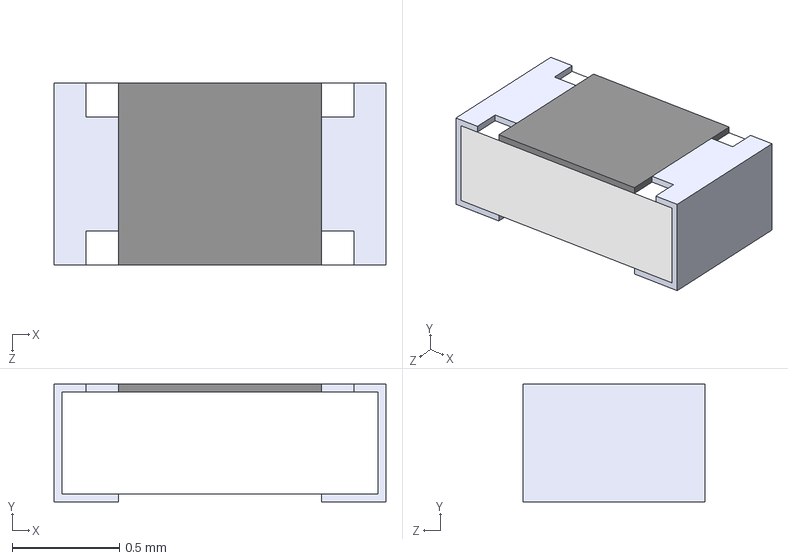
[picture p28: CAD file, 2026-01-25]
boards/ArmEncoderBoard/dependencies/Resistor10K/CRCW060310K0FKEA.step
1.55 x 0.55 x 0.85 mm

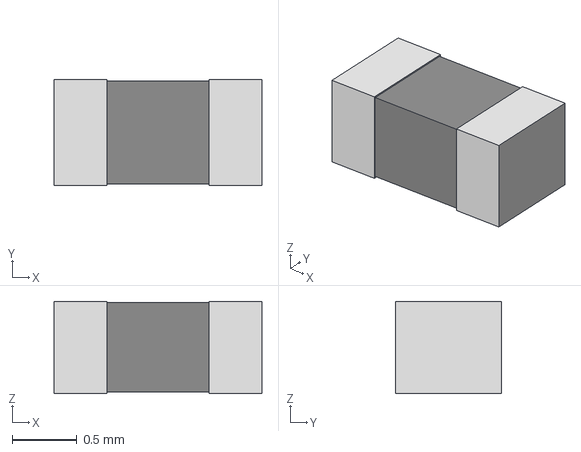
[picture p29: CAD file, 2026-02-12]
boards/ArmEncoderBoard/dependencies/Resistor22/RC0603FR-0722RL.step
1.60 x 0.812 x 0.711 mm

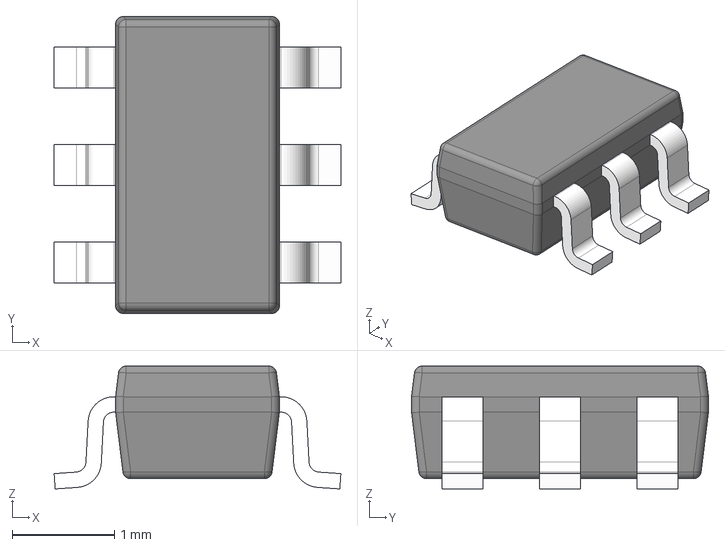
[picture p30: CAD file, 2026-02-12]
boards/ArmEncoderBoard/dependencies/SchmittBuffer/SN74LVC2G17DBVR.stp
2.80 x 2.90 x 1.20 mm
BODY-SOT
LEAD-SOT x 6

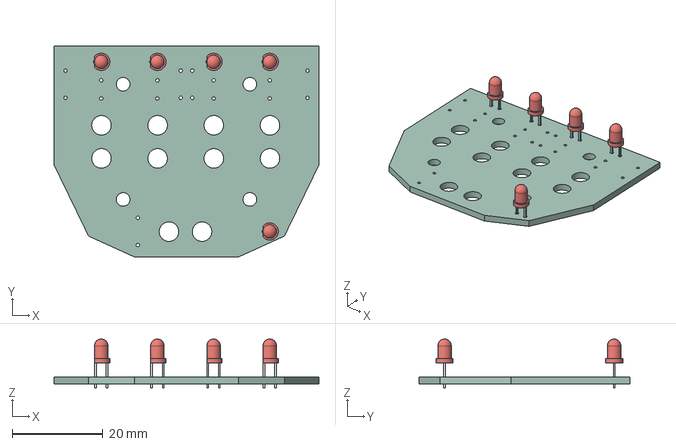
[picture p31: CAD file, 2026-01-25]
boards/ArmPowerBoardWithControls/ArmPowerBoard.step
58.4 x 46.5 x 10.8 mm
ArmPowerBoard PCB

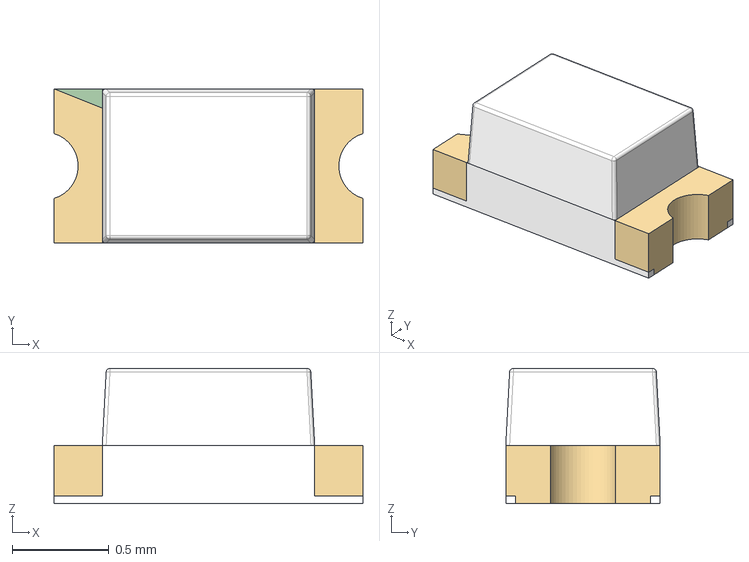
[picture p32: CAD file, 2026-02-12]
boards/ArmRobotBoardTeensy/Dependencies/RedLED/NCD0603R1.stp
1.60 x 0.8 x 0.7 mm

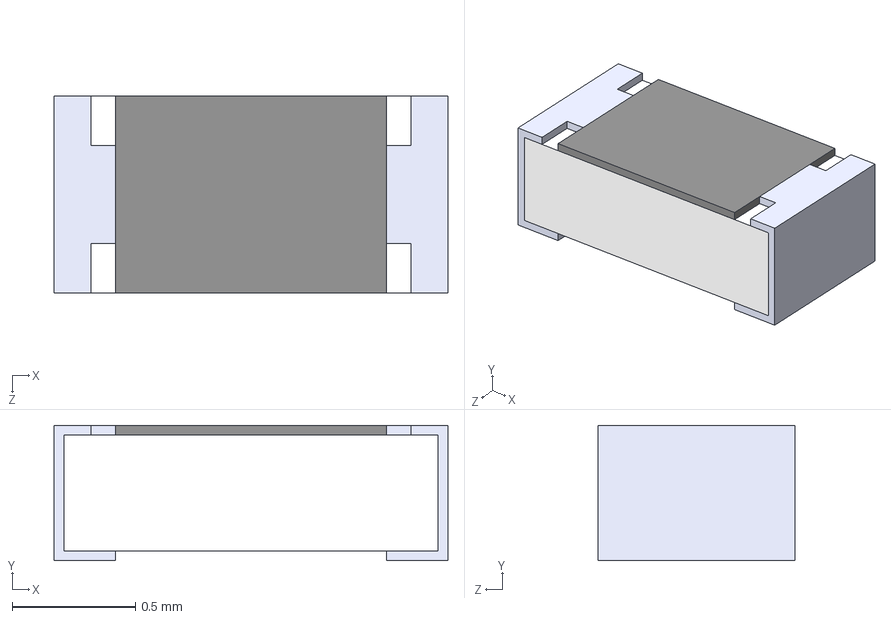
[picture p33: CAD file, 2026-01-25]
boards/ArmRobotBoardTeensy/Dependencies/Resistor5.1K/RC0603FR-075K1L.step
1.60 x 0.55 x 0.8 mm

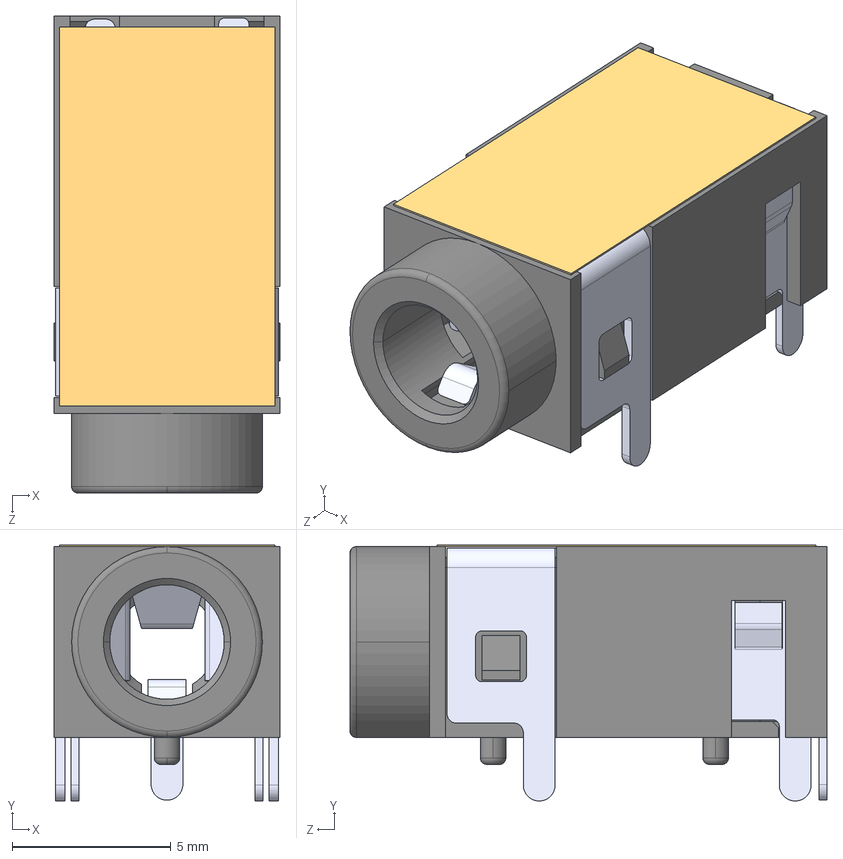
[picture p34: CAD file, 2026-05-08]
boards/AudioBoardTeensy/Dependencies/AudioJack/54-00174.step
7.10 x 8.05 x 15.0 mm
54-00174_housing
54-00174_#1
54-00174_#3
54-00174_#2
54-00174_#4

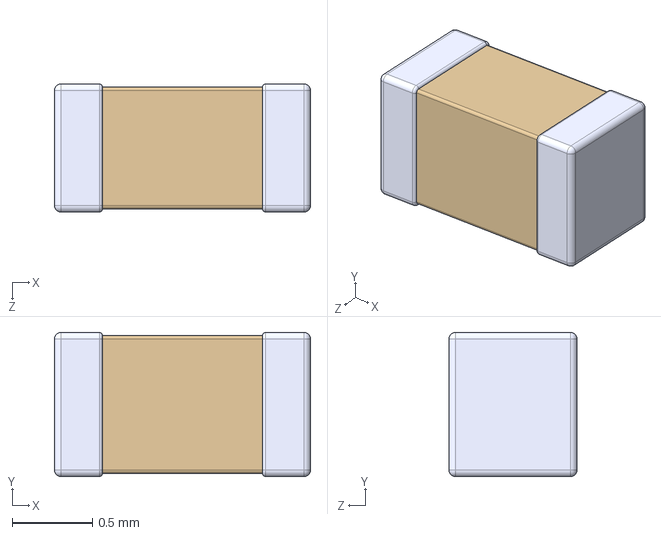
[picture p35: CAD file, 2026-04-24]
boards/AudioBoardTeensy/Dependencies/Capacitor10uF/CL10A106KP8NNNC.step
1.60 x 0.9 x 0.8 mm

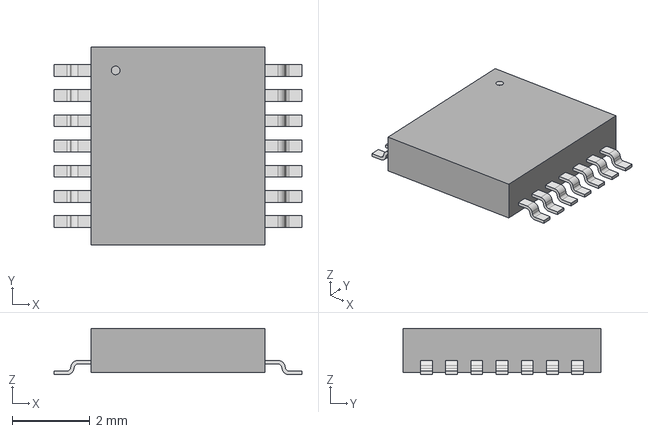
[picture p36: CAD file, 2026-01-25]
boards/LegEncoderBoard/dependencies/AS5047P-ASST/TSSOP-14_AMS.step
6.40 x 5.11 x 1.20 mm

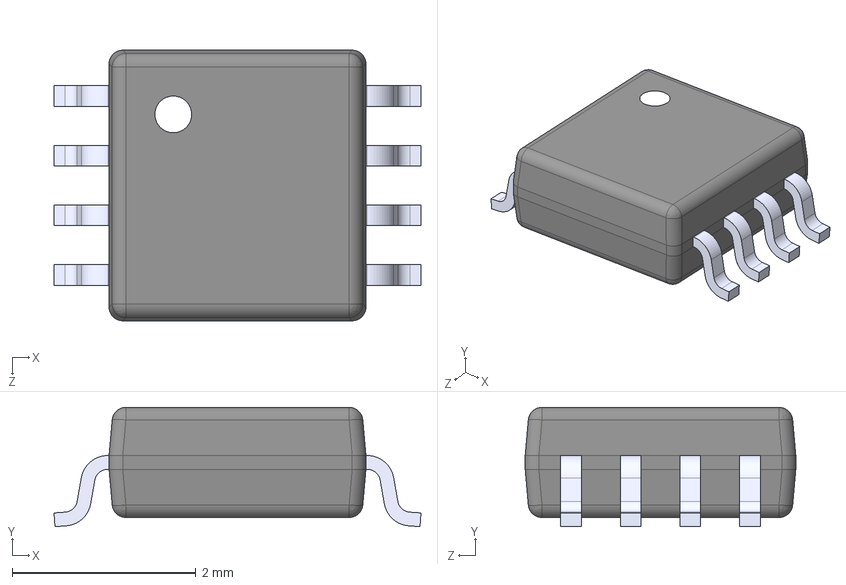
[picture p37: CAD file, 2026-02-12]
boards/LegEncoderBoard/dependencies/SchmittBuffer/SN74LVC3G17DCTR.step
4.00 x 1.30 x 2.95 mm

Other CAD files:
boards/ArmEncoderBoard/dependencies/Resistor470K/RC0603FR-07470KL.step
boards/LegEncoderBoard/dependencies/Capacitor1uF/CC0603JRX7R7BB105.step
boards/LegRobotBoardTeensy/Dependencies/AO3400A/AO3400A.step
boards/ArmEncoderBoard/dependencies/LedBlue/150080BS75000.stp
boards/LegEncoderBoard/dependencies/LedBlue/150080BS75000.stp
boards/LegEncoderBoard/dependencies/Resistor22R/RC0603FR-0722RL.step
boards/LegEncoderBoard/dependencies/Resistor470K/RC0603FR-07470KL.step
boards/LegRobotBoardTeensy/Dependencies/LEDDriver/IS31FL3730-QFLS2-TR.step
boards/LegRobotBoardTeensy/Dependencies/LedRed/XL-1608SURC-06.step
boards/LegRobotBoardTeensy/Dependencies/LevelShifter/74HCT125D.step
boards/LegRobotBoardTeensy/Dependencies/PWMDriver/PCA9685PW,118.step
boards/LegRobotBoardTeensy/Dependencies/Resistor4.7K/CR0603-FX-4701ELF.step
boards/LegRobotBoardTeensy/Dependencies/Resistor47K/RC0603FR-0747KL.step
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

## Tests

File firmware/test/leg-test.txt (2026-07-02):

#include <Wire.h>
#include <Encoder.h>

const int I2C_FREQUENCY_HZ = 400000;      // I2C bus frequency

const int LED_MUX_ADDRESS = 0x34;         // IS31FL3739 I2C address with AD tied to GND

const int FRONT_LEFT_ACTUATOR_POT = 16;   // Front-left actuator feedback pin
const int FRONT_LEFT_WHEEL_A = 32;        // Front-left wheel encoder A
const int FRONT_LEFT_WHEEL_B = 33;        // Front-left wheel encoder B
const int FRONT_LEFT_WHEEL_INDEX = 22;    // Front-left wheel encoder index
const int FRONT_LEFT_WHEEL_EN = 26;       // Front-left wheel driver enable
const int FRONT_LEFT_WHEEL_RPWM = 0;      // Front-left wheel RPWM
const int FRONT_LEFT_WHEEL_LPWM = 1;      // Front-left wheel LPWM
const int FRONT_LEFT_ACTUATOR_EN = 27;    // Front-left actuator driver enable
const int FRONT_LEFT_ACTUATOR_RPWM = 2;   // Front-left actuator RPWM
const int FRONT_LEFT_ACTUATOR_LPWM = 3;   // Front-left actuator LPWM

const int FRONT_RIGHT_ACTUATOR_POT = A17; // Front-right actuator feedback pin
const int FRONT_RIGHT_WHEEL_A = 34;       // Front-right wheel encoder A
const int FRONT_RIGHT_WHEEL_B = 35;       // Front-right wheel encoder B
const int FRONT_RIGHT_WHEEL_INDEX = 23;   // Front-right wheel encoder index
const int FRONT_RIGHT_WHEEL_EN = 28;      // Front-right wheel driver enable
const int FRONT_RIGHT_WHEEL_RPWM = 4;     // Front-right wheel RPWM
const int FRONT_RIGHT_WHEEL_LPWM = 5;     // Front-right wheel LPWM
const int FRONT_RIGHT_ACTUATOR_EN = 29;   // Front-right actuator driver enable
const int FRONT_RIGHT_ACTUATOR_RPWM = 6;  // Front-right actuator RPWM
const int FRONT_RIGHT_ACTUATOR_LPWM = 7;  // Front-right actuator LPWM

const int REAR_LEFT_ACTUATOR_POT = A2;    // Rear-left actuator feedback pin
const int REAR_LEFT_WHEEL_A = 36;         // Rear-left wheel encoder A
const int REAR_LEFT_WHEEL_B = 37;         // Rear-left wheel encoder B
const int REAR_LEFT_WHEEL_INDEX = 24;     // Rear-left wheel encoder index
const int REAR_LEFT_WHEEL_EN = 30;        // Rear-left wheel driver enable
const int REAR_LEFT_WHEEL_RPWM = 8;       // Rear-left wheel RPWM
const int REAR_LEFT_WHEEL_LPWM = 9;       // Rear-left wheel LPWM
const int REAR_LEFT_ACTUATOR_EN = 31;     // Rear-left actuator driver enable
const int REAR_LEFT_ACTUATOR_RPWM = 10;   // Rear-left actuator RPWM
const int REAR_LEFT_ACTUATOR_LPWM = 11;   // Rear-left actuator LPWM

const int REAR_RIGHT_ACTUATOR_POT = A3;   // Rear-right actuator feedback pin
const int REAR_RIGHT_WHEEL_A = 38;        // Rear-right wheel encoder A
const int REAR_RIGHT_WHEEL_B = 39;        // Rear-right wheel encoder B
const int REAR_RIGHT_WHEEL_INDEX = 25;    // Rear-right wheel encoder index
const int REAR_RIGHT_WHEEL_EN = 20;       // Rear-right wheel driver enable
const int REAR_RIGHT_WHEEL_RPWM = 12;     // Rear-right wheel RPWM
const int REAR_RIGHT_WHEEL_LPWM = 13;     // Rear-right wheel LPWM
const int REAR_RIGHT_ACTUATOR_EN = 21;    // Rear-right actuator driver enable
const int REAR_RIGHT_ACTUATOR_RPWM = 14;  // Rear-right actuator RPWM
const int REAR_RIGHT_ACTUATOR_LPWM = 15;  // Rear-right actuator LPWM

const int PWM_MAX = 4095;
const int PWM_HALF = PWM_MAX / 2;
const double ADC_MAX = 4095.0;

const int SERIAL_BAUD = 115200;
const int REPORT_PERIOD_MS = 100;

Encoder wheelEncoder(FRONT_RIGHT_WHEEL_A, FRONT_RIGHT_WHEEL_B);
volatile uint32_t frontLeftIndexRevolutions = 0;

const uint8_t IS31FL3739_PWM_START = 0x03;
const uint8_t IS31FL3739_PWM_END = 0x8F;
const uint8_t IS31FL3739_SCALING_START = 0x92;
const uint8_t IS31FL3739_SCALING_COUNT = 14;
const uint8_t IS31FL3739_CONFIGURATION = 0xA0;
const uint8_t IS31FL3739_GLOBAL_CURRENT = 0xA1;
const uint8_t IS31FL3739_PULL_RESISTORS = 0xB0;
const uint8_t IS31FL3739_PWM_FREQUENCY = 0xB2;
const uint8_t IS31FL3739_RESET = 0xCF;

const uint8_t IS31FL3739_RESET_COMMAND = 0xAE;
const uint8_t IS31FL3739_8_SW_8_CS_NORMAL = 0x11;
const uint8_t IS31FL3739_GLOBAL_CURRENT_TEST = 0x20;
const uint8_t IS31FL3739_2K_PULLS_WHEN_OFF = 0x33;
const uint8_t IS31FL3739_PWM_32_KHZ = 0x01;
const uint8_t LED_FULL_ON = 0xFF;
const uint8_t LED_OFF = 0x00;

const uint8_t DISPLAY_UPDATE_PERIOD_MS = 250;
const uint8_t DISPLAY_0_START_TENTHS = 0;
const uint8_t DISPLAY_1_START_TENTHS = 3;
const uint8_t DISPLAY_2_START_TENTHS = 6;
const uint8_t DISPLAY_3_START_TENTHS = 9;

const uint8_t SEG_A = 1 << 0; // Top of upper square
const uint8_t SEG_B = 1 << 1; // Right of upper square
const uint8_t SEG_C = 1 << 2; // Right of lower square
const uint8_t SEG_D = 1 << 3; // Bottom of lower square
const uint8_t SEG_E = 1 << 4; // Left of lower square
const uint8_t SEG_F = 1 << 5; // Left of upper square
const uint8_t SEG_G = 1 << 6; // Link of both squares
const uint8_t SEG_DP = 1 << 7;

const uint8_t DIGIT_SEGMENTS[] =
{
  SEG_A | SEG_B | SEG_C | SEG_D | SEG_E | SEG_F,         // 0
  SEG_B | SEG_C,                                         // 1
  SEG_A | SEG_B | SEG_D | SEG_E | SEG_G,                 // 2
  SEG_A | SEG_B | SEG_C | SEG_D | SEG_G,                 // 3
  SEG_B | SEG_C | SEG_F | SEG_G,                         // 4
  SEG_A | SEG_C | SEG_D | SEG_F | SEG_G,                 // 5
  SEG_A | SEG_C | SEG_D | SEG_E | SEG_F | SEG_G,         // 6
  SEG_A | SEG_B | SEG_C,                                 // 7
  SEG_A | SEG_B | SEG_C | SEG_D | SEG_E | SEG_F | SEG_G, // 8
  SEG_A | SEG_B | SEG_C | SEG_D | SEG_F | SEG_G          // 9
};

void frontLeftIndexInterrupt()
{
  frontLeftIndexRevolutions++;
}

void writeLedMuxRegister(uint8_t address, uint8_t value)
{
  Wire.beginTransmission(LED_MUX_ADDRESS);
  Wire.write(address);
  Wire.write(value);
  Wire.endTransmission();
}

void fillLedMuxRegisters(uint8_t startAddress, uint8_t count, uint8_t value)
{
  Wire.beginTransmission(LED_MUX_ADDRESS);
  Wire.write(startAddress);

  for (uint8_t index = 0; index < count; index++)
  {
    Wire.write(value);
  }

  Wire.endTransmission();
}

void initializeWheelDisplays()
{
  writeLedMuxRegister(IS31FL3739_RESET, IS31FL3739_RESET_COMMAND);
  delay(1);

  writeLedMuxRegister(IS31FL3739_CONFIGURATION, IS31FL3739_8_SW_8_CS_NORMAL);
  writeLedMuxRegister(IS31FL3739_GLOBAL_CURRENT, IS31FL3739_GLOBAL_CURRENT_TEST);
  writeLedMuxRegister(IS31FL3739_PULL_RESISTORS, IS31FL3739_2K_PULLS_WHEN_OFF);
  writeLedMuxRegister(IS31FL3739_PWM_FREQUENCY, IS31FL3739_PWM_32_KHZ);
  fillLedMuxRegisters(IS31FL3739_SCALING_START, IS31FL3739_SCALING_COUNT, LED_FULL_ON);
  fillLedMuxRegisters(IS31FL3739_PWM_START, IS31FL3739_PWM_END - IS31FL3739_PWM_START + 1, LED_FULL_ON);
}

void writeDisplay(uint8_t display, uint8_t tenths)
{
  const uint8_t leftSw = (display * 2) + 1;
  const uint8_t rightSw = leftSw + 1;
  const uint8_t leftDigit = (tenths >= 10) ? 1 : 0;
  const uint8_t rightDigit = tenths % 10;

  for (uint8_t cs = 1; cs <= 8; cs++)
  {
    uint8_t csOffset = 0x00;

    switch (cs)
    {
      case 1: csOffset = 0x00; break;
      case 2: csOffset = 0x01; break;
      case 3: csOffset = 0x02; break;
      case 4: csOffset = 0x03; break;
      case 5: csOffset = 0x04; break;
      case 6: csOffset = 0x0B; break;
      case 7: csOffset = 0x0C; break;
      default: csOffset = 0x0D; break;
    }

    const uint8_t leftRegister = IS31FL3739_PWM_START + ((leftSw - 1) * 0x10) + csOffset;
    const uint8_t rightRegister = IS31FL3739_PWM_START + ((rightSw - 1) * 0x10) + csOffset;
    const uint8_t leftSegments = DIGIT_SEGMENTS[leftDigit] | SEG_DP;
    const uint8_t rightSegments = DIGIT_SEGMENTS[rightDigit];
    const uint8_t mask = 1 << (cs - 1);

    writeLedMuxRegister(leftRegister, (leftSegments & mask) ? LED_FULL_ON : LED_OFF);
    writeLedMuxRegister(rightRegister, (rightSegments & mask) ? LED_FULL_ON : LED_OFF);
  }
}

void setup()
{
  analogReadResolution(12);
  analogReadAveraging(8);

  pinMode(FRONT_LEFT_WHEEL_EN, OUTPUT);
  pinMode(FRONT_LEFT_ACTUATOR_EN, OUTPUT);
  pinMode(FRONT_RIGHT_WHEEL_EN, OUTPUT);
  pinMode(FRONT_RIGHT_ACTUATOR_EN, OUTPUT);
  pinMode(REAR_LEFT_WHEEL_EN, OUTPUT);
  pinMode(REAR_LEFT_ACTUATOR_EN, OUTPUT);
  pinMode(REAR_RIGHT_WHEEL_EN, OUTPUT);
  pinMode(REAR_RIGHT_ACTUATOR_EN, OUTPUT);

  digitalWrite(FRONT_LEFT_WHEEL_EN, HIGH);
  digitalWrite(FRONT_LEFT_ACTUATOR_EN, HIGH);
  digitalWrite(FRONT_RIGHT_WHEEL_EN, HIGH);
  digitalWrite(FRONT_RIGHT_ACTUATOR_EN, HIGH);
  digitalWrite(REAR_LEFT_WHEEL_EN, HIGH);
  digitalWrite(REAR_LEFT_ACTUATOR_EN, HIGH);
  digitalWrite(REAR_RIGHT_WHEEL_EN, HIGH);
  digitalWrite(REAR_RIGHT_ACTUATOR_EN, HIGH);

  analogWrite(FRONT_LEFT_WHEEL_LPWM, PWM_HALF);
  analogWrite(FRONT_LEFT_WHEEL_RPWM, PWM_HALF);
  analogWrite(FRONT_LEFT_ACTUATOR_LPWM, PWM_HALF);
  analogWrite(FRONT_LEFT_ACTUATOR_RPWM, PWM_HALF);

  analogWrite(FRONT_RIGHT_WHEEL_LPWM, PWM_HALF);
  analogWrite(FRONT_RIGHT_WHEEL_RPWM, PWM_HALF);
  analogWrite(FRONT_RIGHT_ACTUATOR_LPWM, PWM_HALF);
  analogWrite(FRONT_RIGHT_ACTUATOR_RPWM, PWM_HALF);

  analogWrite(REAR_LEFT_WHEEL_LPWM, PWM_HALF);
  analogWrite(REAR_LEFT_WHEEL_RPWM, PWM_HALF);
  analogWrite(REAR_LEFT_ACTUATOR_LPWM, PWM_HALF);
  analogWrite(REAR_LEFT_ACTUATOR_RPWM, PWM_HALF);

  analogWrite(REAR_RIGHT_WHEEL_LPWM, PWM_HALF);
  analogWrite(REAR_RIGHT_WHEEL_RPWM, PWM_HALF);
  analogWrite(REAR_RIGHT_ACTUATOR_LPWM, PWM_HALF);
  analogWrite(REAR_RIGHT_ACTUATOR_RPWM, PWM_HALF);

  Wire.begin();
  Wire.setClock(I2C_FREQUENCY_HZ);

  initializeWheelDisplays();
  writeDisplay(0, DISPLAY_0_START_TENTHS);
  writeDisplay(1, DISPLAY_1_START_TENTHS);
  writeDisplay(2, DISPLAY_2_START_TENTHS);
  writeDisplay(3, DISPLAY_3_START_TENTHS);

  pinMode(FRONT_RIGHT_WHEEL_A, INPUT);
  pinMode(FRONT_RIGHT_WHEEL_B, INPUT);
  pinMode(FRONT_RIGHT_WHEEL_INDEX, INPUT);
  wheelEncoder.write(0);
  attachInterrupt(digitalPinToInterrupt(FRONT_RIGHT_WHEEL_INDEX), frontLeftIndexInterrupt, RISING);

  Serial.begin(SERIAL_BAUD);
  Serial.println("front_left_encoder_test");
  Serial.println("pulses revolutions_from_index");
}

void loop()
{
  static uint32_t lastReport = 0;
  static uint32_t lastDisplayUpdate = 0;
  static uint8_t display0Tenths = DISPLAY_0_START_TENTHS;
  static uint8_t display1Tenths = DISPLAY_1_START_TENTHS;
  static uint8_t display2Tenths = DISPLAY_2_START_TENTHS;
  static uint8_t display3Tenths = DISPLAY_3_START_TENTHS;

  if ((millis() - lastDisplayUpdate) >= DISPLAY_UPDATE_PERIOD_MS)
  {
    lastDisplayUpdate = millis();

    display0Tenths = (display0Tenths + 1) % 11;
    display1Tenths = (display1Tenths + 1) % 11;
    display2Tenths = (display2Tenths + 1) % 11;
    display3Tenths = (display3Tenths + 1) % 11;

    writeDisplay(0, display0Tenths);
    writeDisplay(1, display1Tenths);
    writeDisplay(2, display2Tenths);
    writeDisplay(3, display3Tenths);
  }

  if ((millis() - lastReport) >= REPORT_PERIOD_MS)
  {
    lastReport = millis();

    const int32_t pulses = wheelEncoder.read();

    noInterrupts();
    const uint32_t revolutionsFromIndex = frontLeftIndexRevolutions;
    interrupts();

    Serial.print(pulses);
    Serial.print(" ");
    Serial.println(revolutionsFromIndex);
  }

  delay(1000);
}

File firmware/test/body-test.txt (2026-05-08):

#include <Arduino.h>
#include <Wire.h>
#include <Adafruit_GFX.h>
#include <Adafruit_SSD1306.h>
#include <ShiftRegister74HC595.h>

const int I2C_FREQUENCY = 400000;

const int BUS_CURRENT_SENSOR_PIN = A0;

const int HEAD_PAN_ENABLE = 6;
const int HEAD_PAN_STEP = 24;
const int HEAD_PAN_DIR = 25;
const int HEAD_PAN_ENCODER_STATUS_REGISTER = 11; // U9.QD
const int HEAD_PAN_CS = 0;

const int TORSO_PAN_ENABLE = 7;
const int TORSO_PAN_STATUS = 8;
const int TORSO_PAN_DIR = 20;
const int TORSO_PAN_PWM = 21;
const int TORSO_PAN_ENCODER_STATUS_REGISTER = 10; // U9.QC
const int TORSO_PAN_CS = 1;

const int HEAD_TILT_POTENTIOMETER = A1;
const int HEAD_TILT_MOTOR1_EN = 27;
const int HEAD_TILT_MOTOR1_LPWM = 2;
const int HEAD_TILT_MOTOR1_RPWM = 3;
const int HEAD_TILT_MOTOR2_EN = 28;
const int HEAD_TILT_MOTOR2_LPWM = 4;
const int HEAD_TILT_MOTOR2_RPWM = 5;

const int TORSO_TILT_POTENTIOMETER1 = A2;
const int TORSO_TILT_POTENTIOMETER2 = A3;
const int TORSO_TILT_MOTOR1_EN = 29;
const int TORSO_TILT_MOTOR1_LPWM = 9;
const int TORSO_TILT_MOTOR1_RPWM = 10;
const int TORSO_TILT_MOTOR2_EN = 30;
const int TORSO_TILT_MOTOR2_LPWM = 22;
const int TORSO_TILT_MOTOR2_RPWM = 23;

const int MOUTH_SERVO_SIG = 26;

const int BATTERY_METER_LEVELS = 10;
const int BATTERY_METER_REGISTERS[BATTERY_METER_LEVELS] =
{
  0, // U8.QA
  1, // U8.QB
  2, // U8.QC
  3, // U8.QD
  4, // U8.QE
  5, // U8.QF
  6, // U8.QG
  7, // U8.QH
  8, // U9.QA
  9  // U9.QB
};

const int SHIFT_REGISTER_DATA_PIN = 11;
const int SHIFT_REGISTER_CLOCK_PIN = 13;
const int SHIFT_REGISTER_LATCH_PIN = 31;
const int SHIFT_REGISTER_COUNT = 2;
const int SHIFT_REGISTER_OUTPUT_COUNT = 16;

void setup()
{
    analogReadResolution(12);
    analogReadAveraging(8);

    Wire.begin();
    Wire.setClock(I2C_FREQUENCY);

    pinMode(HEAD_PAN_ENABLE, OUTPUT);
    digitalWrite(HEAD_PAN_ENABLE, HIGH);
    digitalWrite(HEAD_PAN_ENABLE, LOW);
}

void loop()
{
    delay(1000);
}

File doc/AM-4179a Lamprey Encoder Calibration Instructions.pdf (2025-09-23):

### Step 1 -- Inventory your kit

Take care to keep the sensor magnet away from other strong elds. Exposure to Neodynium style magnets can damage the target.

1X Lamprey2 Absolute Encoder Board | 1X Lamprey Ring Magnet

### Step 3 -- Install The Magnet

Install the magnet onto the device you wish to measure. Loctite 401 or similar quick setting glue is recommended.

APPLY GLUE

GENERIC HUB SHOWN
FOR ILLUSTRATION ONLY

SIDE VIEW OF SENSOR AND MAGNET

### Step 4 -- Set The Air Gap

The magnet can be no closer than about 0.09” from the top surface of the board.

The magnet may be placed on either side of the pcb and can be sensed through non-ferrous materials.

### Step 5 -- Install 10-pin IDC cable

This sensor requires 3.3-5v DC. Power can be applied via the USB header, 5x2 header, JST header or the 0.100” header.

5x2 HEADER PIN OUT
SCK | UART -Tx | UART - Rx | ANALOG
| | | OUT | RESET
GND | MOSI | PWM OUT | MISO | 5v In

1

2

9

10

### 6a -- Hold Either Button As You Power Up

This will force the sensor into calibration mode. The sensor will ash all three status LEDs in an ascending pattern. Release the button after the light sequence completes.

### Step 6 -- Basic Sensor Calibration

To use the sensor and receive quality measurements you must complete a calibration once the board and magnet are properly installed. There is a basic and advanced option.

### 6b -- Rotate The Magnet Slowly

Slowly rotate the magnet through at least three complete rotations. The LEDs are now acting as a signal strength indication. They will turn solid as stronger signals are recorded...all three LEDs solid is a maximum signal. At least the red LED solid is required. **A ashing red LED indicates a failure and you should restart the procedure
You have now nished the basic calibration...click either button once to nish. The sensor is now ready!

## Lamprey2 Encoder Assembly Instructions

### Step 7 -- Advanced Sensor Calibration

To enter this mode do a double click at the end of step 6b.
Do an advanced calibration if you desire more precise angle outputs from the sensor. This step requires some careful inputs and is much easier if using the USB connection to view the
debug messages from the sensor. During this step you’ll align the sensor to known angles. The more precisely you align the output during this step the better your result will be. A xture or other means for locking each angle into place is highly recommended.
1. Choose the number of calibration points desired. Each click of the button will cycle through the cal points menu. The LEDs will light to indicate the selected mode. Red = 8, Red+Green = 12, Red + Green + Blue = 24, Blue only = 36. More calibration points will yield a more linear and accurate angle measurment.
2. Do a long press to select your desired calibration. The LEDs will begin ashing.
3. Align your sensor output to an arbitrary zero position and click either button. After each succesful click during this stage the LED’s will ash a sequence to acknowledge that the point has been recorded.
4. Accurately rotate the sensor to your relative angle either CW or CCW, hold it in this position and press either button. The relative angle equals (360 degrees)/(number of cal points). For an eight position cal your relative angle between points would be 45 degrees.
5. Repeat step 4. for the total number of cal points chosen.
**The sensor will only record points that are within a certain tolerance range...the sensor will quickly ash all the LEDs to indicate that you’ve attempted to select a point that is out of range.
6. When complete the status LEDs will ash an ascending sequence and the sensor will wake into 3.3v analog output mode. You should see the always on power LED and the blue LED illuminated. Any other LED indication means the calibration failed and you should restart.

### Step 2 -- Mount The Sensor Board

The sensor should be as concentric as possible with the planned axis of rotation of the target magnet.

#10 SOCKET OR

BUTTON HEAD

GENERIC GEARBOX SHOWN
FOR ILLUSTRATION ONLY

### Setting New Zero Positions

To set a new zero position during normal operation press and hold either user button for one second.
The LEDs will ash to indicate a new setting.
The red LED will ash when you cross the zero point to oer a visual check of the programmed location.

1X 10-pin Cable

## Lamprey2 Encoder Calibration Instructions

0.090”

*RxTx lines are disconnected by default solder pads are availble on the board to connect these lines into the 5x2 if needed

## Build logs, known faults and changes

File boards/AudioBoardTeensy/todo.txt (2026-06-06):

Swap AUDIO and GND on schematic and board

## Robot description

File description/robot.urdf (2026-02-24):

<?xml version="1.0" ?>
<robot name="str1ker">

    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

    <link name="world" />
    <link name="base_link">
        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
        <inertial>
            <origin rpy="0 0 0" xyz="-0.07311604 0.00008330 0.03705764" />
            <mass value="0.70818404" />
            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
        </inertial>
    </link>
    <link name="shoulder_link">
        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
        <inertial>
            <origin rpy="0 0 0" xyz="0.01708182 0.02587065 -0.00000217" />
            <mass value="0.38358403" />
            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
        </inertial>
    </link>
    <link name="upperarm_link">
        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
        <inertial>
            <origin rpy="0 0 0" xyz="0.19665771 -0.00446385 0.00009568" />
            <mass value="1.13853115" />
            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
        </inertial>
    </link>
    <link name="forearm_link">
        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
        <inertial>
            <origin rpy="0 0 0" xyz="0.20328210 -0.00230698 -0.00000001" />
            <mass value="0.63998399" />
            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
        </inertial>
    </link>
    <link name="drumstick_link">
        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
        <inertial>
            <origin rpy="0 0 0" xyz="0.04484721 -0.00013749 -0.00008218" />
            <mass value="0.07166651" />
            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
        </inertial>
    </link>
    <link name="tip_link">
        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
    </link>
    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

    <link name="upperarm_actuator_body_link">
        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
        <inertial>
            <origin rpy="0 0 0" xyz="0.06788886 -0.01642314 0" />
            <mass value="0.70647685" />
            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
        </inertial>
    </link>
    <link name="upperarm_actuator_shaft_link">
        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
        <inertial>
            <mass value="0.04967122" />
            <origin rpy="0 0 0" xyz="0.03254861 0.00000005 -0.00000010" />
            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
        </inertial>
    </link>
    <link name="forearm_actuator_body_link">
        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
        <inertial>
            <mass value="0.76281631" />
            <origin rpy="0 0 0" xyz="0.09092269 0.00010124 -0.00000002" />
            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
        </inertial>
    </link>
    <link name="forearm_actuator_shaft_link">
        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
        <inertial>
            <mass value="0.08789688" />
            <origin rpy="0 0 0" xyz="0.03195776 0.00000003 0" />
            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
        </inertial>
    </link>
    <link name="forearm_actuator_connector_link">
        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
        <inertial>
            <mass value="0.01257956" />
            <origin rpy="0 0 0" xyz="-0.02406711 0 0" />
            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
        </inertial>
    </link>
    <link name="solenoid_mount_link">
        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
        <inertial>
            <mass value="0.1" />
            <origin xyz="0 0 0" rpy="0 0 0" />
            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
        </inertial>
    </link>
    <link name="solenoid_shaft_link">
        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
        <inertial>
            <mass value="0.1" />
            <origin xyz="0 0 0" rpy="0 0 0" />
            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
        </inertial>
    </link>

    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

    <joint name="fixed" type="fixed">
        <origin rpy="0 0 0" xyz="0 0 0.5" />
        <parent link="world" />
        <child link="base_link" />
    </joint>
    <joint name="base" type="revolute">
        <origin rpy="1.5708 0 0" xyz="0 0 0" />
        <axis xyz="0 1 0" />
        <parent link="base_link" />
        <child link="shoulder_link" />
        <limit effort="100" velocity="3.14160" lower="-1.5708" upper="1.5708" />
        <dynamics damping="5" friction="5" />
    </joint>
    <joint name="shoulder" type="revolute">
        <origin rpy="0 0 0" xyz="-0.013 0.109 0.0" />
        <axis xyz="0 0 1" />
        <parent link="shoulder_link" />
        <child link="upperarm_link" />
        <limit effort="100" velocity="1.0" lower="0.404676" upper="0.813453" />
        <dynamics damping="0.7" friction="1.4" />
        <mimic joint="upperarm_actuator" multiplier="7.640691589" offset="0.817273346" />
    </joint>
    <joint name="elbow" type="revolute">
        <origin rpy="0 0 0" xyz="0.4173 0 0" />
        <axis xyz="0 0 1" />
        <parent link="upperarm_link" />
        <child link="forearm_link" />
        <limit effort="100" velocity="1.0" lower="-1.93302196" upper="-1.123992" />
        <dynamics damping="0.7" friction="1.4" />
        <mimic joint="forearm_actuator" multiplier="15.925786614" offset="-1.123992" />
    </joint>
    <joint name="wrist" type="revolute">
        <origin rpy="0 0 0" xyz="0.48059393086 0 -0.023" />
        <axis xyz="0 0 1" />
        <parent link="forearm_link" />
        <child link="drumstick_link" />
        <limit effort="100" velocity="1.0" lower="0.959931" upper="1.0" />
        <dynamics damping="0.7" friction="1.4" />
        <mimic joint="solenoid" multiplier="13.8167" offset="0.9862" />
    </joint>
    <joint name="tip" type="fixed">
        <origin rpy="0 0 0" xyz="0.305 0.0 0.0" />
        <parent link="drumstick_link" />
        <child link="tip_link" />
    </joint>

    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

    <joint name="upperarm_actuator_mount" type="revolute">
        <origin rpy="0 0 0" xyz="0.101045 -0.0504975 0" />
        <axis xyz="0 0 1" />
        <parent link="shoulder_link" />
        <child link="upperarm_actuator_body_link" />
        <limit effort="100" velocity="1.0" lower="-6" upper="6" />
        <dynamics damping="0.7" friction="1.4" />
        <mimic joint="upperarm_actuator" multiplier="0.9" offset="1.560796327" />
    </joint>
    <joint name="upperarm_actuator" type="prismatic">
        <origin rpy="0 0 0" xyz="0.153 -0.002 0" />
        <axis xyz="1 0 0" />
        <parent link="upperarm_actuator_body_link" />
        <child link="upperarm_actuator_shaft_link" />
        <limit effort="100" velocity="0.0508" lower="-0.054" upper="-0.0005" />
        <dynamics damping="0.7" friction="1.4" />
    </joint>
    <joint name="forearm_actuator_mount" type="revolute">
        <origin rpy="0 0 0" xyz="0.130 -0.034 0" />
        <axis xyz="0 0 1" />
        <parent link="upperarm_link" />
        <child link="forearm_actuator_body_link" />
        <limit effort="100" velocity="1.0" lower="-6" upper="6" />
        <dynamics damping="0.7" friction="1.4" />
        <mimic joint="forearm_actuator" multiplier="-2.5" offset="-0.146602" />
    </joint>
    <joint name="forearm_actuator" type="prismatic">
        <origin rpy="0 0 0" xyz="0.210 0 0" />
        <axis xyz="1 0 0" />
        <parent link="forearm_actuator_body_link" />
        <child link="forearm_actuator_shaft_link" />
        <limit effort="100" velocity="0.0109982" lower="-0.0508" upper="0" />
        <dynamics damping="0.7" friction="1.4" />
    </joint>
    <joint name="forearm_actuator_connector" type="revolute">
        <origin rpy="0 0 0" xyz="0.0605718 0.004 0" />
        <axis xyz="0 0 1" />
        <parent link="forearm_link" />
        <child link="forearm_actuator_connector_link" />
        <limit effort="100" velocity="1.0" lower="1.5137" upper="1.5444" />
        <dynamics damping="0.7" friction="1.4" />
        <mimic joint="forearm_actuator" multiplier="0.604330709" offset="1.5444" />
    </joint>
    <joint name="solenoid_mount" type="fixed">
        <origin rpy="0 0 0" xyz="0.355 -0.031 0.013" />
        <axis xyz="0 0 1" />
        <parent link="forearm_link" />
        <child link="solenoid_mount_link" />
        <limit effort="100" velocity="1.0" lower="-0.09" upper="-0.09" />
        <dynamics damping="0.7" friction="1.4" />
    </joint>
    <joint name="solenoid" type="prismatic">
        <origin rpy="0 0 0" xyz="0 0 0" />
        <axis xyz="1 0 0" />
        <parent link="solenoid_mount_link" />
        <child link="solenoid_shaft_link" />
        <limit effort="100" velocity="1.0" lower="-0.0019" upper="0.001" />
        <dynamics damping="0.7" friction="1.4" />
    </joint>
    
    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
</robot>

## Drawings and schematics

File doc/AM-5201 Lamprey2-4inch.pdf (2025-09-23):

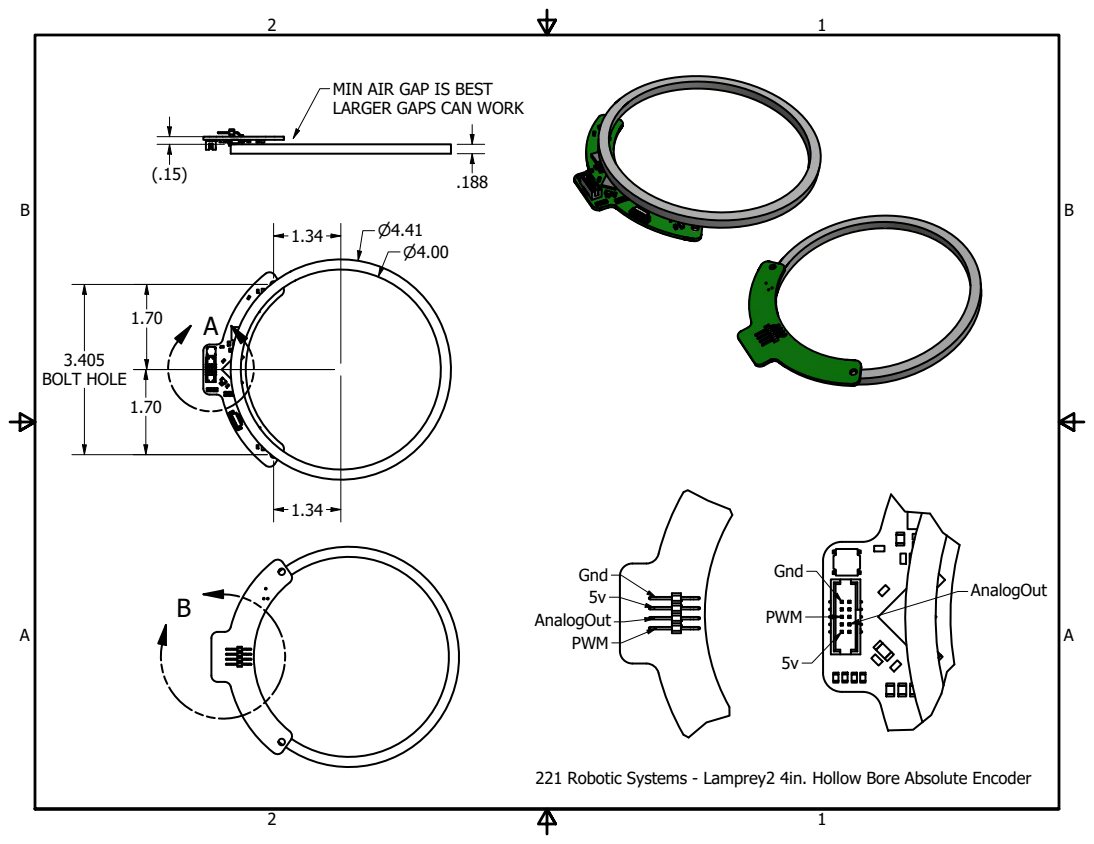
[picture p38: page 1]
BOLT HOLE

MIN AIR GAP IS BEST
LARGER GAPS CAN WORK

221 Robotic Systems - Lamprey2 4in. Hollow Bore Absolute Encoder

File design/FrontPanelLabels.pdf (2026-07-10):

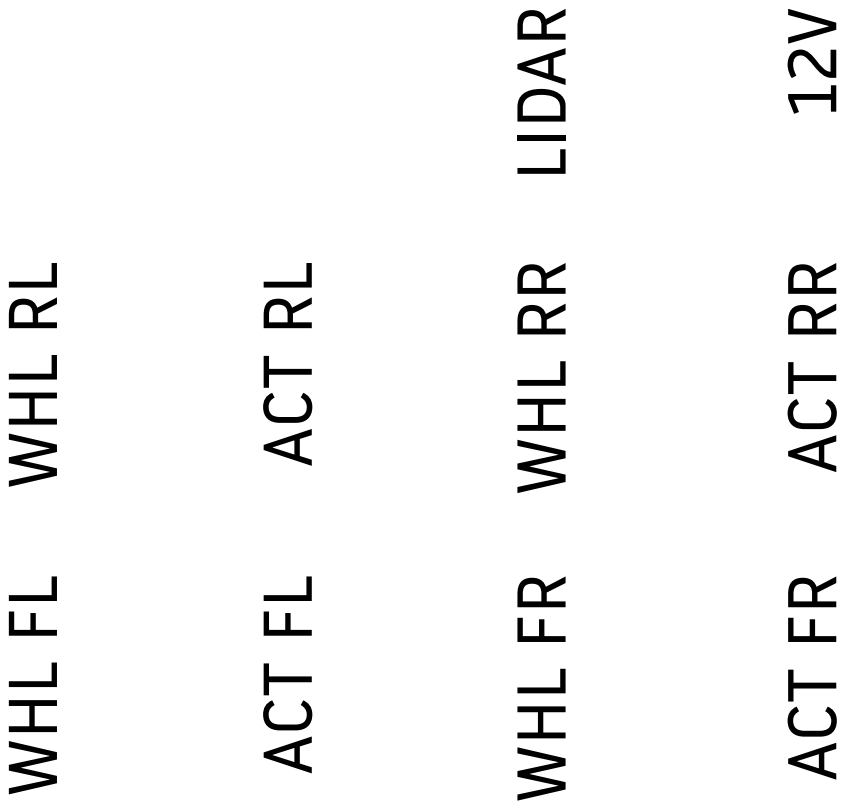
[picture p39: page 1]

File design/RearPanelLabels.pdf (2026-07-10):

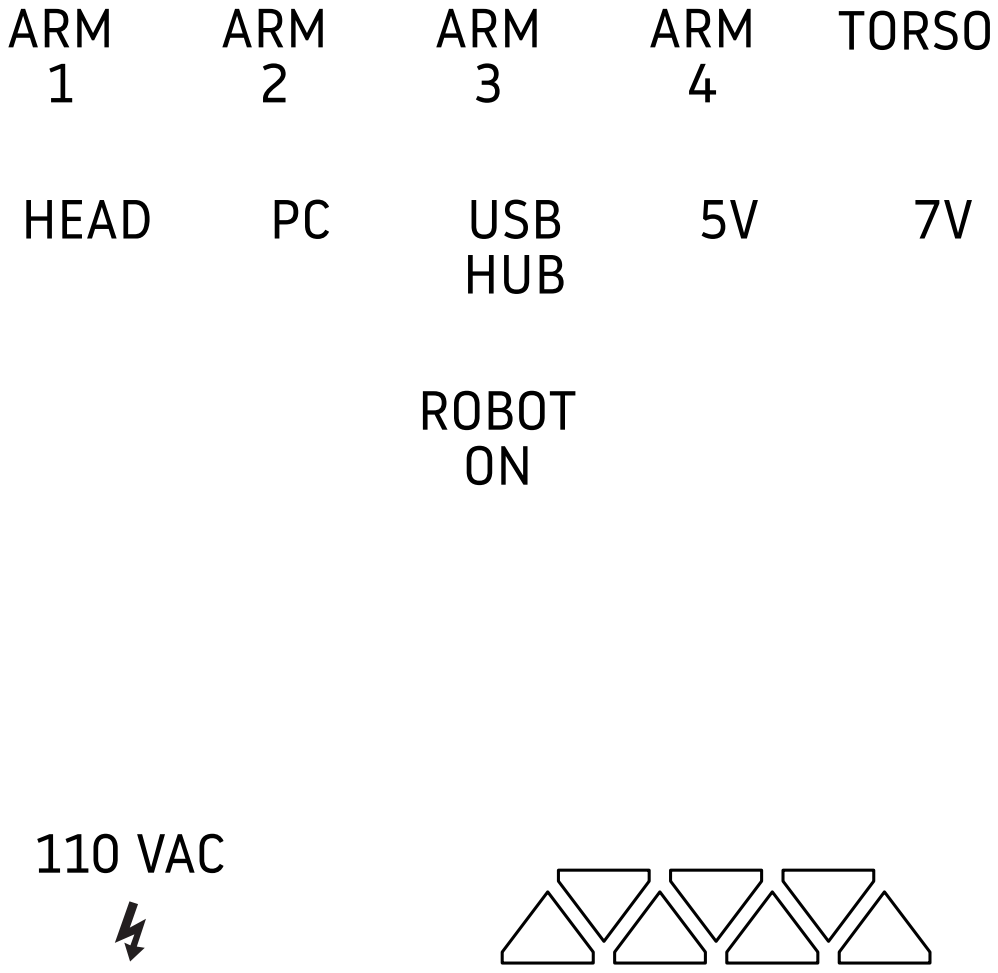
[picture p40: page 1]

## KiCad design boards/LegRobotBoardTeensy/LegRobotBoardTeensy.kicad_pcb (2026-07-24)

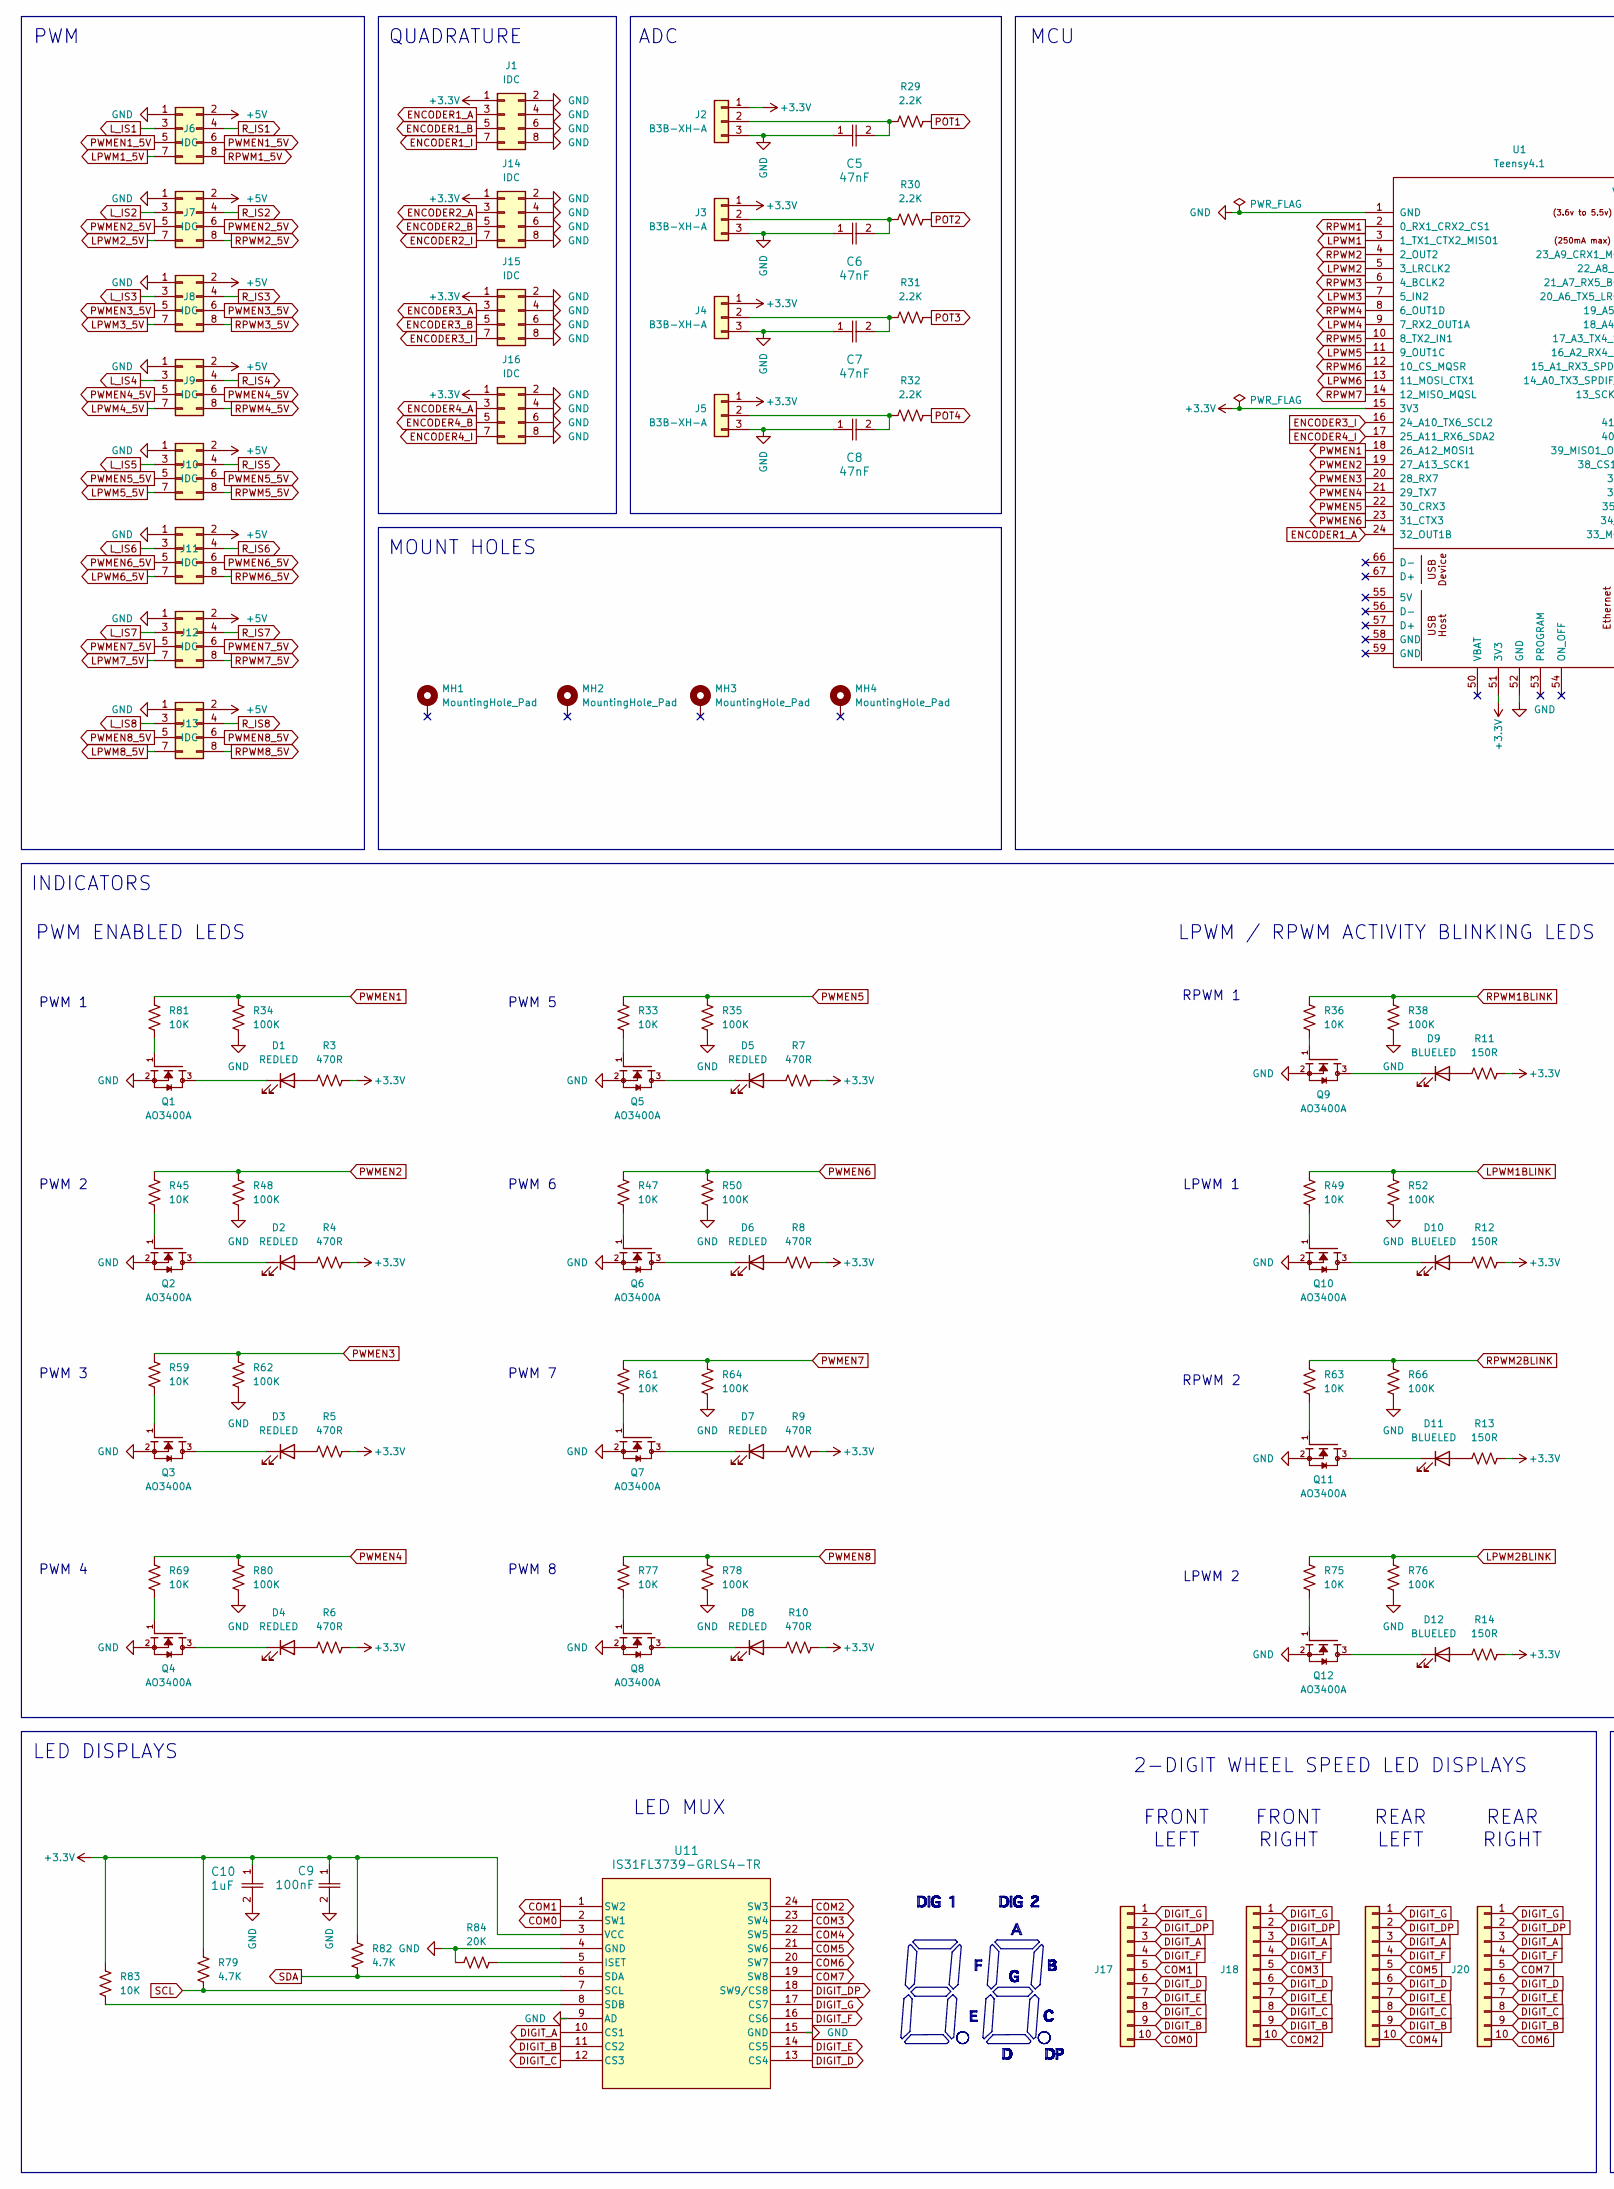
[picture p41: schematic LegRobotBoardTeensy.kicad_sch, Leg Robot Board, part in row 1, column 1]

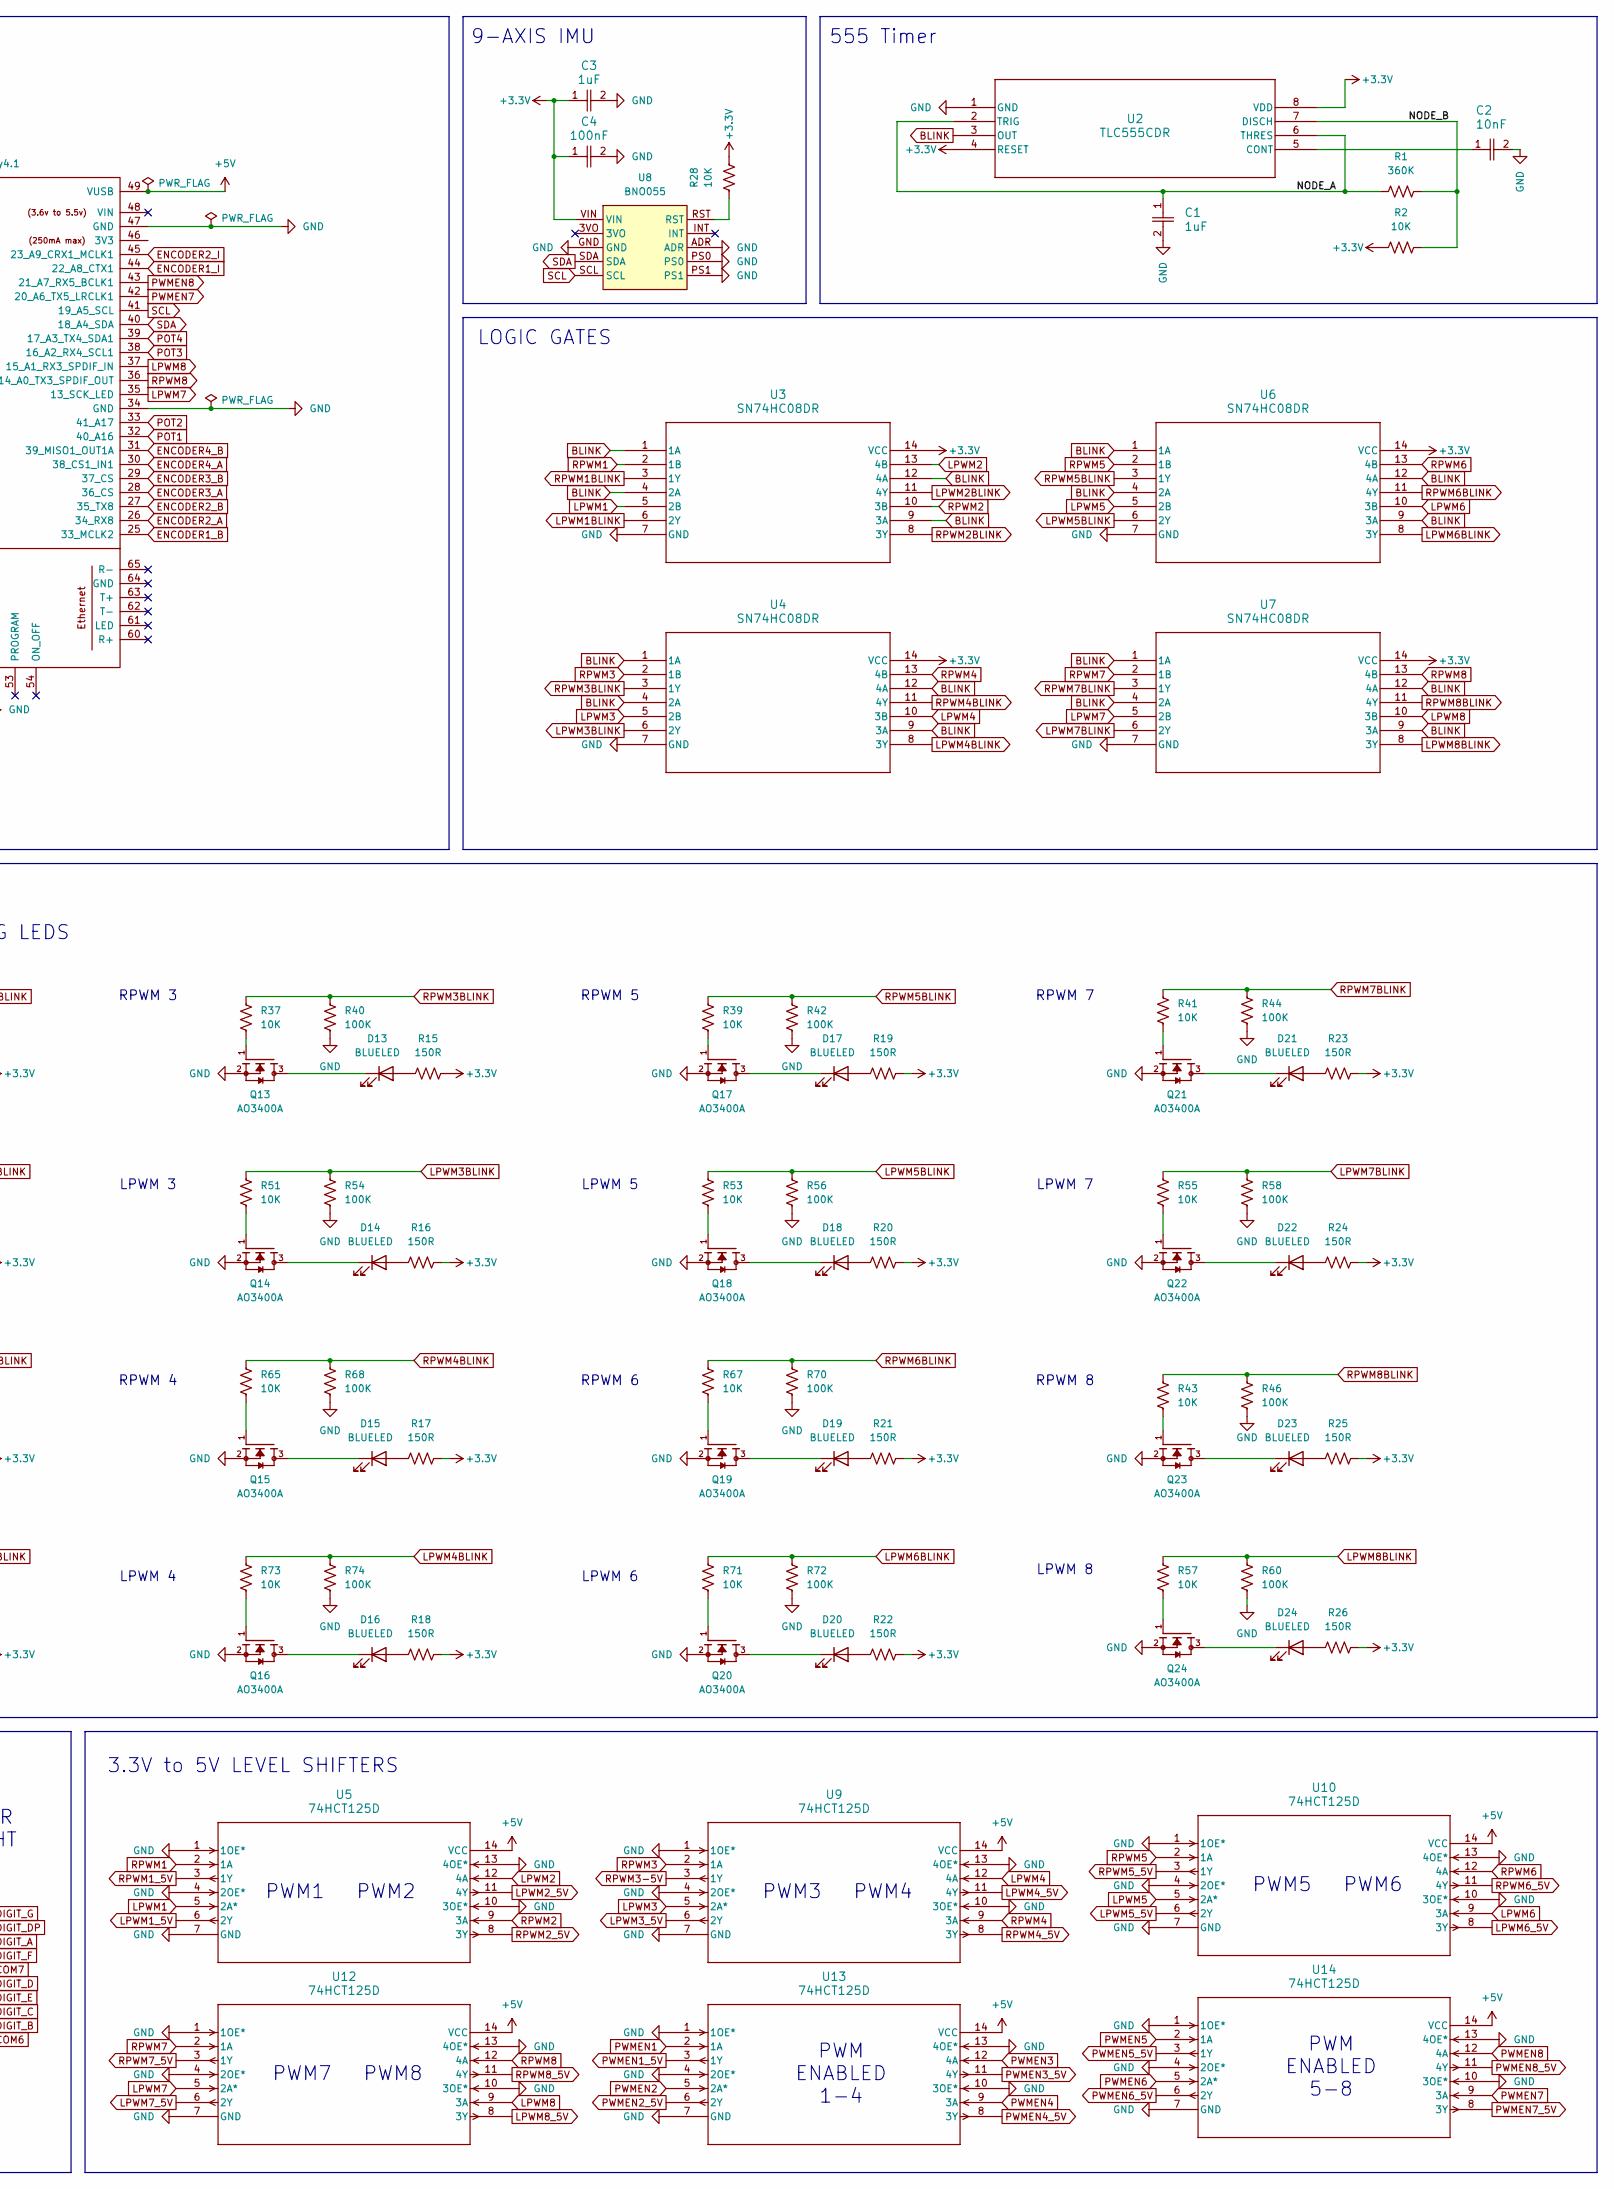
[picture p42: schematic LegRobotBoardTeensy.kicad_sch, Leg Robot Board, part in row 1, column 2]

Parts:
C1, C3: 1uF; CC0603JRX7R7BB105; LCSC C519560
C2: 10nF; C0402C103J4RACTU; LCSC C2167451
C4, C9: 100nF; CC0603KRX7R9BB104; LCSC C14663
C5, C6, C7, C8: 47nF; CAPC1608X90N; LCSC C1622
C10: 1uF; CC0603JRX7R7BB105; LCSC C2167451
D1, D2, D3, D4, D5, D6, D7, D8: REDLED; XL-1608SURC-06; LCSC C965799
D9, D10, D11, D12, D13, D14, D15, D16, D17, D18, D19, D20, D21, D22, D23, D24: BLUELED; 150080BS75000_Modified; LCSC C6067133
J1, J6, J7, J8, J9, J10, J11, J12, J13, J14, J15, J16: IDC; IDC-Header_2x04_P2.54mm_Vertical
J2, J3, J4, J5: B3B-XH-A; JST_XH_B3B-XH-A_1x03_P2.50mm_Vertical
J17, J18, J19, J20: Conn_01x10; DIP-10_W10.16mm
MH1, MH2, MH3, MH4: MountingHole_Pad; MountingHole_3.2mm_M3_ISO7380_Pad
Q1, Q2, Q3, Q4, Q5, Q6, Q7, Q8, Q9, Q10, Q11, Q12, Q13, Q14, Q15, Q16, Q17, Q18, Q19, Q20, Q21, Q22, Q23, Q24: AO3400A; LCSC C20917
R1: 360K; RC0603FR-07360KL; LCSC C137740
R2, R28, R33, R36, R37, R39, R41, R43, R45, R47, R49, R51, R53, R55, R57, R59, R61, R63, R65, R67, R69, R71, R73, R75, R77, R81, R83: 10K; CRCW060310K0FKEA; LCSC C844918
R3, R4, R5, R6, R7, R8, R9, R10: 470R; RC0603FR-07470RL; LCSC C114669
R11, R12, R13, R14, R15, R16, R17, R18, R19, R20, R21, R22, R23, R24, R25, R26: 150R; RESC1607X60N; LCSC C114608
R29, R30, R31, R32: 2.2K; RC0603FR-072K2L; LCSC C114662
R34, R35, R38, R40, R42, R44, R46, R48, R50, R52, R54, R56, R58, R60, R62, R64, R66, R68, R70, R72, R74, R76, R78, R80: 100K; CRCW0603100KFKEA; LCSC C844916
R79, R82: 4.7K; CR0603-FX-4701ELF; LCSC C17673
R84: 20K; CRCW060310K0FKEA; LCSC C5123585
U1: Teensy4.1; Teensy41
U2: TLC555CDR; LCSC C6986
U3, U4, U6, U7: SN74HC08DR; LCSC C337768
U5, U9, U10, U12, U13, U14: 74HCT125D; LCSC C5962
U8: BNO055
U11: IS31FL3739-GRLS4-TR; IS31FL3730-QFLS2-TR

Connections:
+3.3V: C3.1, C4.1, C9.1, C10.1, J1.1, J2.1, J3.1, J4.1, J5.1, J14.1, J15.1, J16.1, R2.1, R3.2, R4.2, R5.2, R6.2, R7.2, R8.2, R9.2, R10.2, R11.2, R12.2, R13.2, R14.2, R15.2, R16.2, R17.2, R18.2, R19.2, R20.2, R21.2, R22.2, R23.2, R24.2, R25.2, R26.2, R28.2, R79.1, R82.1, R83.1, U1.15 (3V3), U1.51 (3V3), U2.4 (RESET), U2.8 (VDD), U3.14 (VCC), U4.14 (VCC), U6.14 (VCC), U7.14 (VCC), U8.VIN, U11.3 (VCC)
+5V: J6.2, J7.2, J8.2, J9.2, J10.2, J11.2, J12.2, J13.2, U1.49 (VUSB), U5.14 (VCC), U9.14 (VCC), U10.14 (VCC), U12.14 (VCC), U13.14 (VCC), U14.14 (VCC)
/NODE_A: C1.1, R1.1, U2.2 (TRIG), U2.6 (THRES)
/NODE_B: R1.2, R2.2, U2.7 (DISCH)
BLINK: U2.3 (OUT), U3.1 (1A), U3.4 (2A), U3.9 (3A), U3.12 (4A), U4.1 (1A), U4.4 (2A), U4.9 (3A), U4.12 (4A), U6.1 (1A), U6.4 (2A), U6.9 (3A), U6.12 (4A), U7.1 (1A), U7.4 (2A), U7.9 (3A), U7.12 (4A)
COM0: J17.10, U11.2 (SW1)
COM1: J17.5, U11.1 (SW2)
COM2: J18.10, U11.24 (SW3)
COM3: J18.5, U11.23 (SW4)
COM4: J19.10, U11.22 (SW5)
COM5: J19.5, U11.21 (SW6)
COM6: J20.10, U11.20 (SW7)
COM7: J20.5, U11.19 (SW8)
DIGIT_A: J17.3, J18.3, J19.3, J20.3, U11.10 (CS1)
DIGIT_B: J17.9, J18.9, J19.9, J20.9, U11.11 (CS2)
DIGIT_C: J17.8, J18.8, J19.8, J20.8, U11.12 (CS3)
DIGIT_D: J17.6, J18.6, J19.6, J20.6, U11.13 (CS4)
DIGIT_DP: J17.2, J18.2, J19.2, J20.2, U11.18 (SW9/CS8)
DIGIT_E: J17.7, J18.7, J19.7, J20.7, U11.14 (CS5)
DIGIT_F: J17.4, J18.4, J19.4, J20.4, U11.16 (CS6)
DIGIT_G: J17.1, J18.1, J19.1, J20.1, U11.17 (CS7)
ENCODER1_A: J1.3, U1.24 (32_OUT1B)
ENCODER1_B: J1.5, U1.25 (33_MCLK2)
ENCODER1_I: J1.7, U1.44 (22_A8_CTX1)
ENCODER2_A: J14.3, U1.26 (34_RX8)
ENCODER2_B: J14.5, U1.27 (35_TX8)
ENCODER2_I: J14.7, U1.45 (23_A9_CRX1_MCLK1)
ENCODER3_A: J15.3, U1.28 (36_CS)
ENCODER3_B: J15.5, U1.29 (37_CS)
ENCODER3_I: J15.7, U1.16 (24_A10_TX6_SCL2)
ENCODER4_A: J16.3, U1.30 (38_CS1_IN1)
ENCODER4_B: J16.5, U1.31 (39_MISO1_OUT1A)
ENCODER4_I: J16.7, U1.17 (25_A11_RX6_SDA2)
GND: C1.2, C2.2, C3.2, C4.2, C5.1, C6.1, C7.1, C8.1, C9.2, C10.2, J1.2, J1.4, J1.6, J1.8, J2.3, J3.3, J4.3, J5.3, J6.1, J7.1, J8.1, J9.1, J10.1, J11.1, J12.1, J13.1, J14.2, J14.4, J14.6, J14.8, J15.2, J15.4, J15.6, J15.8, J16.2, J16.4, J16.6, J16.8, Q1.2, Q2.2, Q3.2, Q4.2, Q5.2, Q6.2, Q7.2, Q8.2, Q9.2, Q10.2, Q11.2, Q12.2, Q13.2, Q14.2, Q15.2, Q16.2, Q17.2, Q18.2, Q19.2, Q20.2, Q21.2, Q22.2, Q23.2, Q24.2, R34.2, R35.2, R38.2, R40.2, R42.2, R44.2, R46.2, R48.2, R50.2, R52.2, R54.2, R56.2, R58.2, R60.2, R62.2, R64.2, R66.2, R68.2, R70.2, R72.2, R74.2, R76.2, R78.2, R80.2, R84.1, U1.1 (GND), U1.34 (GND), U1.47 (GND), U1.52 (GND), U2.1 (GND), U3.7 (GND), U4.7 (GND), U5.1 (1OE*), U5.4 (2OE*), U5.7 (GND), U5.10 (3OE*), U5.13 (4OE*), U6.7 (GND), U7.7 (GND), U8.ADR, U8.GND, U8.PS0, U8.PS1, U9.1 (1OE*), U9.4 (2OE*), U9.7 (GND), U9.10 (3OE*), U9.13 (4OE*), U10.1 (1OE*), U10.4 (2OE*), U10.7 (GND), U10.10 (3OE*), U10.13 (4OE*), U11.4 (GND), U11.9 (AD), U11.15 (GND), U12.1 (1OE*), U12.4 (2OE*), U12.7 (GND), U12.10 (3OE*), U12.13 (4OE*), U13.1 (1OE*), U13.4 (2OE*), U13.7 (GND), U13.10 (3OE*), U13.13 (4OE*), U14.1 (1OE*), U14.4 (2OE*), U14.7 (GND), U14.10 (3OE*), U14.13 (4OE*)
LPWM1: U1.3 (1_TX1_CTX2_MISO1), U3.5 (2B), U5.5 (2A*)
LPWM1BLINK: R49.1, R52.1, U3.6 (2Y)
LPWM1_5V: J6.7, U5.6 (2Y)
LPWM2: U1.5 (3_LRCLK2), U3.13 (4B), U5.12 (4A)
LPWM2BLINK: R75.1, R76.1, U3.11 (4Y)
LPWM2_5V: J7.7, U5.11 (4Y)
LPWM3: U1.7 (5_IN2), U4.5 (2B), U9.5 (2A*)
LPWM3BLINK: R51.1, R54.1, U4.6 (2Y)
LPWM3_5V: J8.7, U9.6 (2Y)
LPWM4: U1.9 (7_RX2_OUT1A), U4.10 (3B), U9.12 (4A)
LPWM4BLINK: R73.1, R74.1, U4.8 (3Y)
LPWM4_5V: J9.7, U9.11 (4Y)
LPWM5: U1.11 (9_OUT1C), U6.5 (2B), U10.5 (2A*)
LPWM5BLINK: R53.1, R56.1, U6.6 (2Y)
LPWM5_5V: J10.7, U10.6 (2Y)
LPWM6: U1.13 (11_MOSI_CTX1), U6.10 (3B), U10.9 (3A)
LPWM6BLINK: R71.1, R72.1, U6.8 (3Y)
LPWM6_5V: J11.7, U10.8 (3Y)
LPWM7: U1.35 (13_SCK_LED), U7.5 (2B), U12.5 (2A*)
LPWM7BLINK: R55.1, R58.1, U7.6 (2Y)
LPWM7_5V: J12.7, U12.6 (2Y)
LPWM8: U1.37 (15_A1_RX3_SPDIF_IN), U7.10 (3B), U12.9 (3A)
LPWM8BLINK: R57.1, R60.1, U7.8 (3Y)
LPWM8_5V: J13.7, U12.8 (3Y)
L_IS1: J6.3
L_IS2: J7.3
L_IS3: J8.3
L_IS4: J9.3
L_IS5: J10.3
L_IS6: J11.3
L_IS7: J12.3
L_IS8: J13.3
unnamed: D1.2 (A), R3.1
unnamed: D1.1 (K), Q1.3
unnamed: D2.2 (A), R4.1
unnamed: D2.1 (K), Q2.3
unnamed: D3.2 (A), R5.1
unnamed: D3.1 (K), Q3.3
unnamed: D4.2 (A), R6.1
unnamed: D4.1 (K), Q4.3
unnamed: D5.2 (A), R7.1
unnamed: D5.1 (K), Q5.3
unnamed: D6.2 (A), R8.1
unnamed: D6.1 (K), Q6.3
unnamed: D7.2 (A), R9.1
unnamed: D7.1 (K), Q7.3
unnamed: D8.2 (A), R10.1
unnamed: D8.1 (K), Q8.3
unnamed: D9.2 (A), R11.1
unnamed: D9.1 (K), Q9.3
unnamed: D10.2 (A), R12.1
unnamed: D10.1 (K), Q10.3
unnamed: D11.2 (A), R13.1
unnamed: D11.1 (K), Q11.3
unnamed: D12.2 (A), R14.1
unnamed: D12.1 (K), Q12.3
unnamed: D13.2 (A), R15.1
unnamed: D13.1 (K), Q13.3
unnamed: D14.2 (A), R16.1
unnamed: D14.1 (K), Q14.3
unnamed: D15.2 (A), R17.1
unnamed: D15.1 (K), Q15.3
unnamed: D16.2 (A), R18.1
unnamed: D16.1 (K), Q16.3
unnamed: D17.2 (A), R19.1
unnamed: D17.1 (K), Q17.3
unnamed: D18.2 (A), R20.1
unnamed: D18.1 (K), Q18.3
unnamed: D19.2 (A), R21.1
unnamed: D19.1 (K), Q19.3
unnamed: D20.2 (A), R22.1
unnamed: D20.1 (K), Q20.3
unnamed: D21.2 (A), R23.1
unnamed: D21.1 (K), Q21.3
unnamed: D22.2 (A), R24.1
unnamed: D22.1 (K), Q22.3
unnamed: D23.2 (A), R25.1
unnamed: D23.1 (K), Q23.3
unnamed: D24.2 (A), R26.1
unnamed: D24.1 (K), Q24.3
unnamed: C5.2, J2.2, R29.1
unnamed: C6.2, J3.2, R30.1
unnamed: C7.2, J4.2, R31.1
unnamed: C8.2, J5.2, R32.1
unnamed: Q1.1, R81.2
unnamed: Q2.1, R45.2
unnamed: Q3.1, R59.2
unnamed: Q4.1, R69.2
unnamed: Q5.1, R33.2
unnamed: Q6.1, R47.2
unnamed: Q7.1, R61.2
unnamed: Q8.1, R77.2
unnamed: Q9.1, R36.2
unnamed: Q10.1, R49.2
unnamed: Q11.1, R63.2
unnamed: Q12.1, R75.2
unnamed: Q13.1, R37.2
unnamed: Q14.1, R51.2
unnamed: Q15.1, R65.2
unnamed: Q16.1, R73.2
unnamed: Q17.1, R39.2
unnamed: Q18.1, R53.2
unnamed: Q19.1, R67.2
unnamed: Q20.1, R71.2
unnamed: Q21.1, R41.2
unnamed: Q22.1, R55.2
unnamed: Q23.1, R43.2
unnamed: Q24.1, R57.2
unnamed: R28.1, U8.RST
unnamed: C2.1, U2.5 (CONT)
unnamed: R84.2, U11.5 (ISET)
unnamed: R83.2, U11.8 (SDB)
POT1: R29.2, U1.32 (40_A16)
POT2: R30.2, U1.33 (41_A17)
POT3: R31.2, U1.38 (16_A2_RX4_SCL1)
POT4: R32.2, U1.39 (17_A3_TX4_SDA1)
PWMEN1: R34.1, R81.1, U1.18 (26_A12_MOSI1), U13.2 (1A)
PWMEN1_5V: J6.5, J6.6, U13.3 (1Y)
PWMEN2: R45.1, R48.1, U1.19 (27_A13_SCK1), U13.5 (2A*)
PWMEN2_5V: J7.5, J7.6, U13.6 (2Y)
PWMEN3: R59.1, R62.1, U1.20 (28_RX7), U13.12 (4A)
PWMEN3_5V: J8.5, J8.6, U13.11 (4Y)
PWMEN4: R69.1, R80.1, U1.21 (29_TX7), U13.9 (3A)
PWMEN4_5V: J9.5, J9.6, U13.8 (3Y)
PWMEN5: R33.1, R35.1, U1.22 (30_CRX3), U14.2 (1A)
PWMEN5_5V: J10.5, J10.6, U14.3 (1Y)
PWMEN6: R47.1, R50.1, U1.23 (31_CTX3), U14.5 (2A*)
PWMEN6_5V: J11.5, J11.6, U14.6 (2Y)
PWMEN7: R61.1, R64.1, U1.42 (20_A6_TX5_LRCLK1), U14.9 (3A)
PWMEN7_5V: J12.5, J12.6, U14.8 (3Y)
PWMEN8: R77.1, R78.1, U1.43 (21_A7_RX5_BCLK1), U14.12 (4A)
PWMEN8_5V: J13.5, J13.6, U14.11 (4Y)
RPWM1: U1.2 (0_RX1_CRX2_CS1), U3.2 (1B), U5.2 (1A)
RPWM1BLINK: R36.1, R38.1, U3.3 (1Y)
RPWM1_5V: J6.8, U5.3 (1Y)
RPWM2: U1.4 (2_OUT2), U3.10 (3B), U5.9 (3A)
RPWM2BLINK: R63.1, R66.1, U3.8 (3Y)
RPWM2_5V: J7.8, U5.8 (3Y)
RPWM3: U1.6 (4_BCLK2), U4.2 (1B), U9.2 (1A)
RPWM3-5V: U9.3 (1Y)
RPWM3BLINK: R37.1, R40.1, U4.3 (1Y)
RPWM3_5V: J8.8
RPWM4: U1.8 (6_OUT1D), U4.13 (4B), U9.9 (3A)
RPWM4BLINK: R65.1, R68.1, U4.11 (4Y)
RPWM4_5V: J9.8, U9.8 (3Y)
RPWM5: U1.10 (8_TX2_IN1), U6.2 (1B), U10.2 (1A)
RPWM5BLINK: R39.1, R42.1, U6.3 (1Y)
RPWM5_5V: J10.8, U10.3 (1Y)
RPWM6: U1.12 (10_CS_MQSR), U6.13 (4B), U10.12 (4A)
RPWM6BLINK: R67.1, R70.1, U6.11 (4Y)
RPWM6_5V: J11.8, U10.11 (4Y)
RPWM7: U1.14 (12_MISO_MQSL), U7.2 (1B), U12.2 (1A)
RPWM7BLINK: R41.1, R44.1, U7.3 (1Y)
RPWM7_5V: J12.8, U12.3 (1Y)
RPWM8: U1.36 (14_A0_TX3_SPDIF_OUT), U7.13 (4B), U12.12 (4A)
RPWM8BLINK: R43.1, R46.1, U7.11 (4Y)
RPWM8_5V: J13.8, U12.11 (4Y)
R_IS1: J6.4
R_IS2: J7.4
R_IS3: J8.4
R_IS4: J9.4
R_IS5: J10.4
R_IS6: J11.4
R_IS7: J12.4
R_IS8: J13.4
SCL: R79.2, U1.41 (19_A5_SCL), U8.SCL, U11.7 (SCL)
SDA: R82.2, U1.40 (18_A4_SDA), U8.SDA, U11.6 (SDA)

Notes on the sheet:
FRONT LEFT
PWM 5
LPWM 6
PWM1
LOGIC GATES
9-AXIS IMU
LED MUX
RPWM 3
PWM7
RPWM 5
LED DISPLAYS
3.3V to 5V LEVEL SHIFTERS
RPWM 7
LPWM 5
QUADRATURE
ADC
PWM
PWM 8
PWM4
PWM 2
MOUNT HOLES
LPWM 3
LPWM 7
555 Timer
MCU
RPWM 1
PWM 7
PWM ENABLED 5-8
PWM 1
PWM 3
PWM8
PWM 6
REAR RIGHT
REAR LEFT
PWM ENABLED LEDS
FRONT RIGHT
LPWM 8
LPWM 2
PWM2
PWM6

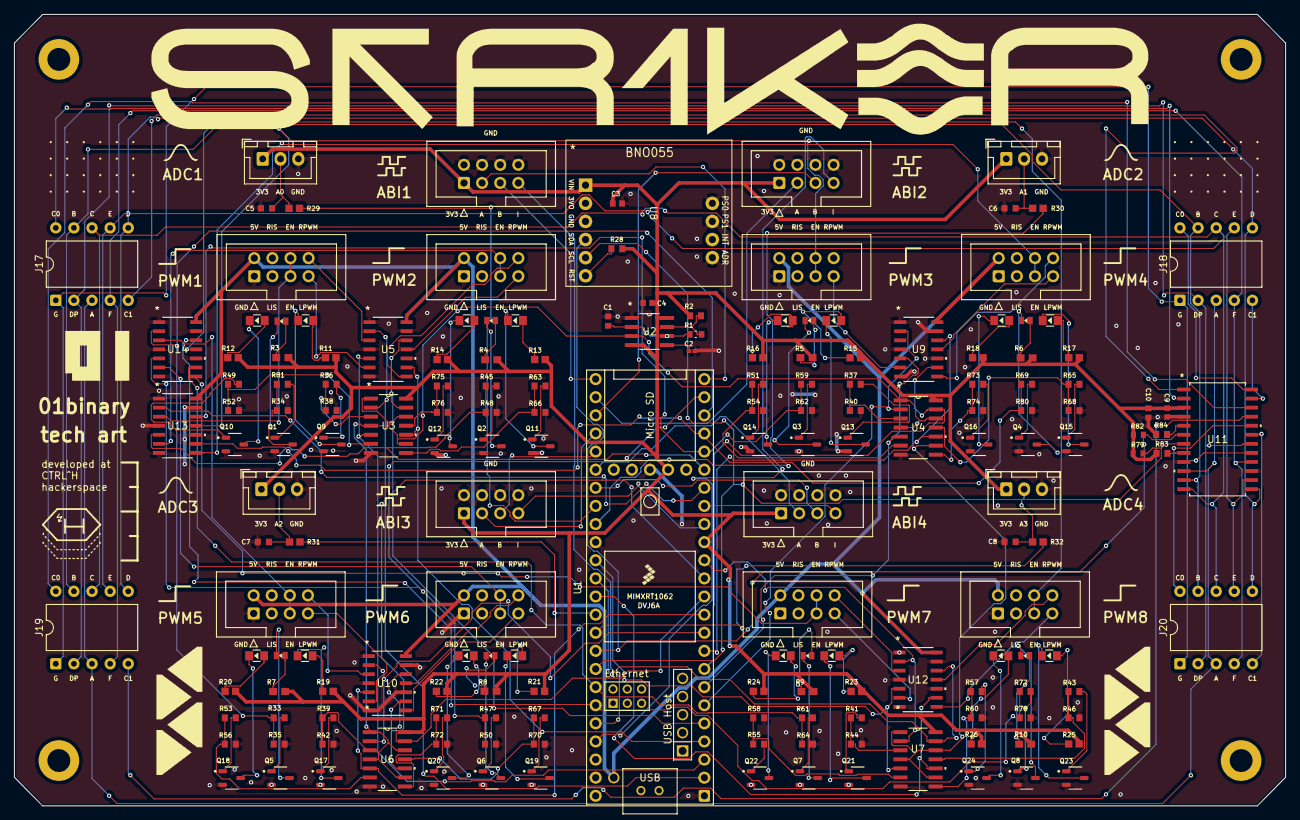
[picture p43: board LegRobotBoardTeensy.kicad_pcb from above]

Board: 2 copper layers, 178.2 x 110.9 mm, 179 parts (0 on the bottom side), 183 nets.

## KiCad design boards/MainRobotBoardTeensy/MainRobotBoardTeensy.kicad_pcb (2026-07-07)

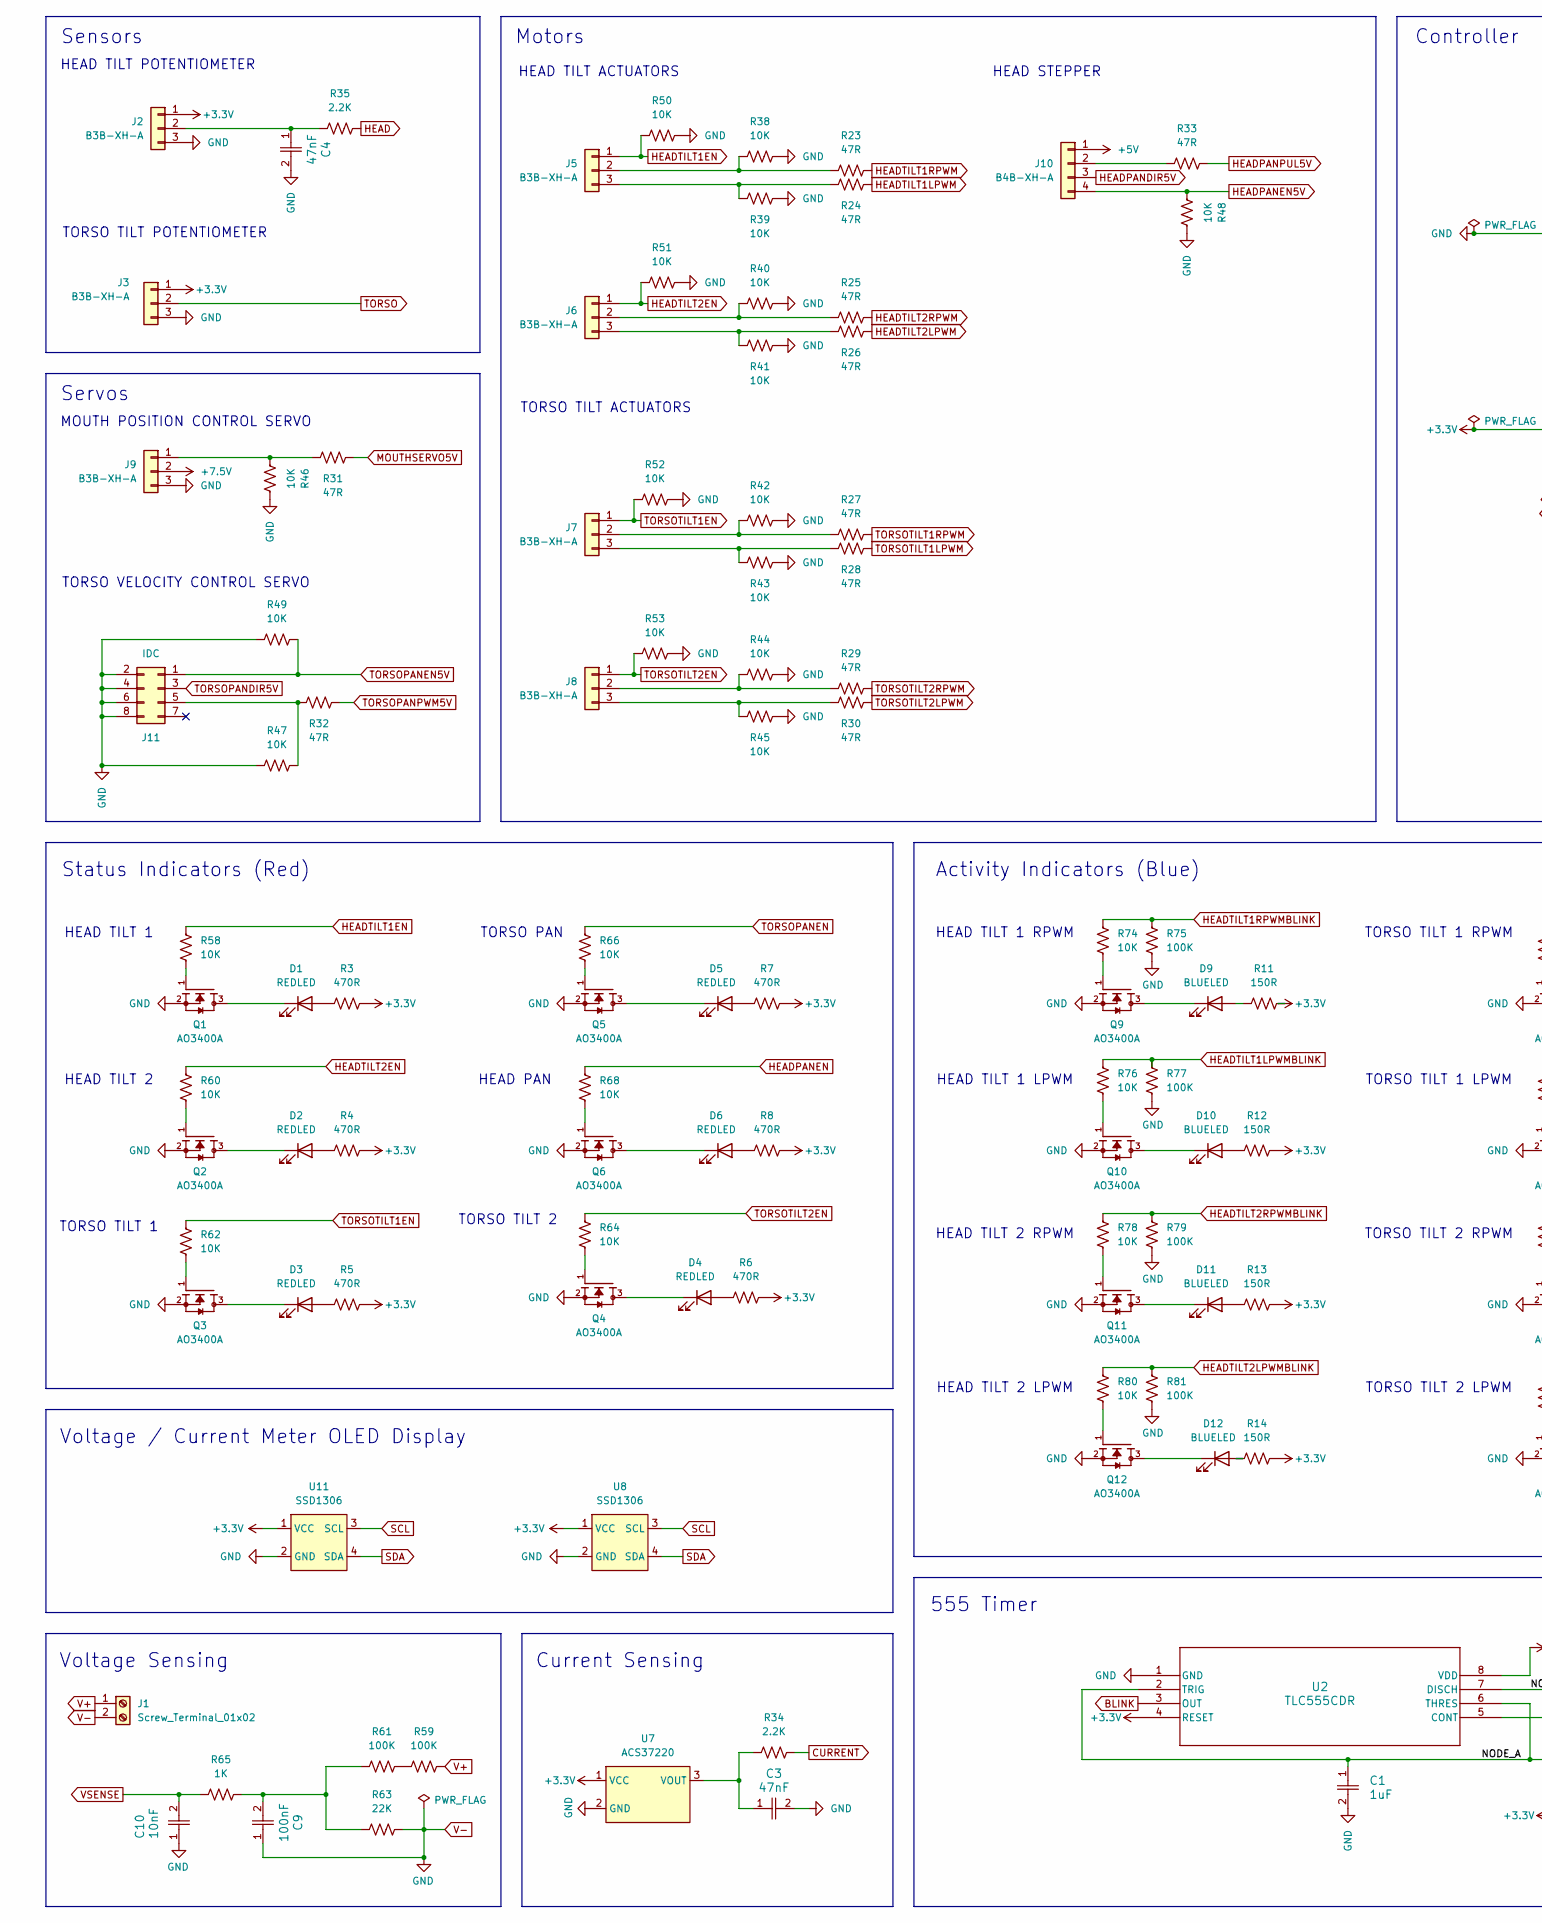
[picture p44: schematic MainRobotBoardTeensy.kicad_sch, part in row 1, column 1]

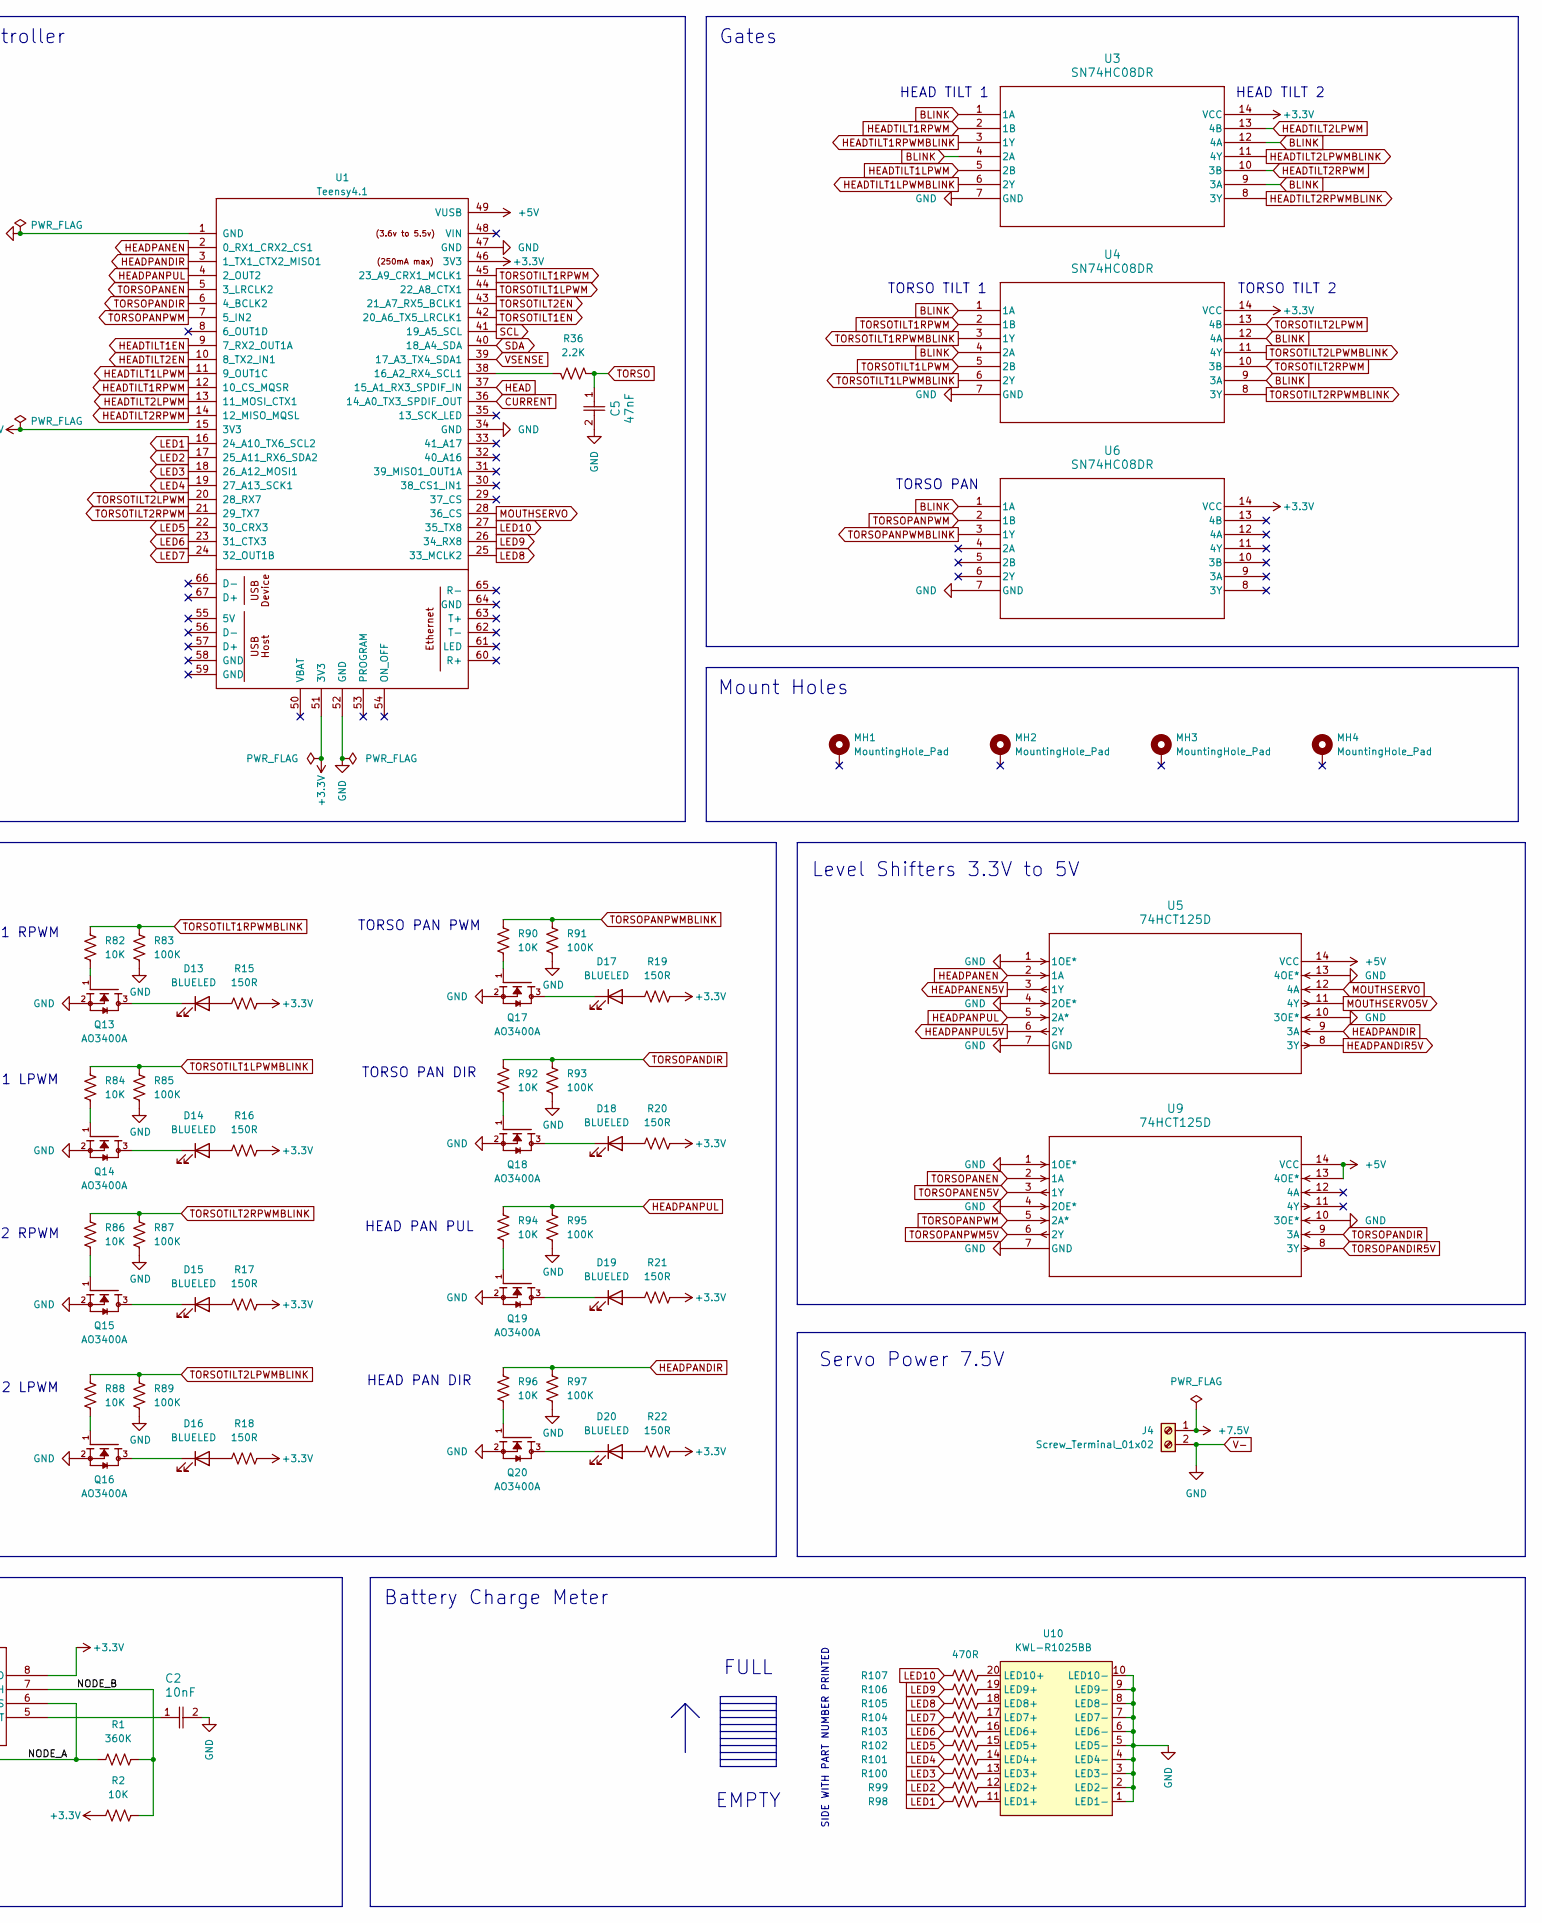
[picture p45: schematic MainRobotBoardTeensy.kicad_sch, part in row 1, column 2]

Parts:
C1: 1uF; CC0603JRX7R7BB105; LCSC C519560
C2, C10: 10nF; C0402C103J4RACTU; LCSC C152817
C3, C4, C5: 47nF; CAPC1608X90N; LCSC C1622
C9: 100nF; CC0603KRX7R9BB104; LCSC C14663
D1, D2, D3, D4, D5, D6: REDLED; XL-1608SURC-06; LCSC C965799
D9, D10, D11, D12, D13, D14, D15, D16, D17, D18, D19, D20: BLUELED; 150080BS75000_Modified; LCSC C6067133
J1, J4: Screw_Terminal_01x02; TerminalBlock_Phoenix_MKDS-1,5-2-5.08_1x02_P5.08mm_Horizont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
J2, J3, J5, J6, J7, J8, J9: B3B-XH-A; JST_XH_B3B-XH-A_1x03_P2.50mm_Vertical
J10: B4B-XH-A; JST_XH_B4B-XH-A_1x04_P2.50mm_Vertical
J11: IDC; IDC-Header_2x04_P2.54mm_Vertical
MH1, MH2, MH3, MH4: MountingHole_Pad; MountingHole_3.2mm_M3_ISO7380_Pad
Q1, Q2, Q3, Q4, Q5, Q6, Q9, Q10, Q11, Q12, Q13, Q14, Q15, Q16, Q17, Q18, Q19, Q20: AO3400A; LCSC C20917
R1: 360K; RC0603FR-07360KL; LCSC C137740
R2, R38, R39, R40, R41, R42, R43, R44, R45, R46, R47, R48, R49, R50, R51, R52, R53, R58, R60, R62, R64, R66, R68, R74, R76, R78, R80, R82, R84, R86, R88, R90, R92, R94, R96: 10K; CRCW060310K0FKEA; LCSC C844918
R3, R4, R5, R6, R7, R8, R98, R99, R100, R101, R102, R103, R104, R105, R106, R107: 470R; RC0603FR-07470RL; LCSC C114669
R11, R12, R13, R14, R15, R16, R17, R18, R19, R20, R21, R22: 150R; RESC1607X60N; LCSC C114608
R23, R24, R25, R26, R27, R28, R29, R30, R31, R32, R33: 47R; RESC1608X55; LCSC C114623
R34, R35, R36: 2.2K; RC0603FR-072K2L; LCSC C114662
R59, R61, R75, R77, R79, R81, R83, R85, R87, R89, R91, R93, R95, R97: 100K; CRCW0603100KFKEA; LCSC C844916
R63: 22K; 0603WAF2202T5E; LCSC C31850
R65: 1K; RCG06031K00FKEA; LCSC C4264491
U1: Teensy4.1; Teensy41
U2: TLC555CDR; LCSC C6986
U3, U4, U6: SN74HC08DR; LCSC C337768
U5, U9: 74HCT125D
U7: ACS37220
U8, U11: SSD1306
U10: KWL-R1025BB

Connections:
+3.3V: J2.1, J3.1, R2.1, R3.2, R4.2, R5.2, R6.2, R7.2, R8.2, R11.2, R12.2, R13.2, R14.2, R15.2, R16.2, R17.2, R18.2, R19.2, R20.2, R21.2, R22.2, U1.15 (3V3), U1.46 (3V3), U1.51 (3V3), U2.4 (RESET), U2.8 (VDD), U3.14 (VCC), U4.14 (VCC), U6.14 (VCC), U7.1 (VCC), U8.1 (VCC), U11.1 (VCC)
+5V: J10.1, U1.49 (VUSB), U5.14 (VCC), U9.13 (4OE*), U9.14 (VCC)
+7.5V: J4.1, J9.2
/NODE_A: C1.1, R1.1, U2.2 (TRIG), U2.6 (THRES)
/NODE_B: R1.2, R2.2, U2.7 (DISCH)
BLINK: U2.3 (OUT), U3.1 (1A), U3.4 (2A), U3.9 (3A), U3.12 (4A), U4.1 (1A), U4.4 (2A), U4.9 (3A), U4.12 (4A), U6.1 (1A)
CURRENT: R34.2, U1.36 (14_A0_TX3_SPDIF_OUT)
HEAD: R35.2, U1.37 (15_A1_RX3_SPDIF_IN)
HEADPANDIR: R96.1, R97.1, U1.3 (1_TX1_CTX2_MISO1), U5.9 (3A)
HEADPANDIR5V: J10.3, U5.8 (3Y)
HEADPANEN: R68.1, U1.2 (0_RX1_CRX2_CS1), U5.2 (1A)
HEADPANEN5V: J10.4, R48.1, U5.3 (1Y)
HEADPANPUL: R94.1, R95.1, U1.4 (2_OUT2), U5.5 (2A*)
HEADPANPUL5V: R33.2, U5.6 (2Y)
HEADTILT1EN: J5.1, R50.1, R58.1, U1.9 (7_RX2_OUT1A)
HEADTILT1LPWM: R24.2, U1.11 (9_OUT1C), U3.5 (2B)
HEADTILT1LPWMBLINK: R76.1, R77.1, U3.6 (2Y)
HEADTILT1RPWM: R23.2, U1.12 (10_CS_MQSR), U3.2 (1B)
HEADTILT1RPWMBLINK: R74.1, R75.1, U3.3 (1Y)
HEADTILT2EN: J6.1, R51.1, R60.1, U1.10 (8_TX2_IN1)
HEADTILT2LPWM: R26.2, U1.13 (11_MOSI_CTX1), U3.13 (4B)
HEADTILT2LPWMBLINK: R80.1, R81.1, U3.11 (4Y)
HEADTILT2RPWM: R25.2, U1.14 (12_MISO_MQSL), U3.10 (3B)
HEADTILT2RPWMBLINK: R78.1, R79.1, U3.8 (3Y)
LED1: R98.2, U1.16 (24_A10_TX6_SCL2)
LED2: R99.2, U1.17 (25_A11_RX6_SDA2)
LED3: R100.2, U1.18 (26_A12_MOSI1)
LED4: R101.2, U1.19 (27_A13_SCK1)
LED5: R102.2, U1.22 (30_CRX3)
LED6: R103.2, U1.23 (31_CTX3)
LED7: R104.2, U1.24 (32_OUT1B)
LED8: R105.2, U1.25 (33_MCLK2)
LED9: R106.2, U1.26 (34_RX8)
LED10: R107.2, U1.27 (35_TX8)
MOUTHSERVO: U1.28 (36_CS), U5.12 (4A)
MOUTHSERVO5V: R31.2, U5.11 (4Y)
unnamed: C9.2, R61.1, R63.1, R65.2
unnamed: D1.2 (A), R3.1
unnamed: D1.1 (K), Q1.3
unnamed: D2.2 (A), R4.1
unnamed: D2.1 (K), Q2.3
unnamed: D3.2 (A), R5.1
unnamed: D3.1 (K), Q3.3
unnamed: D4.2 (A), R6.1
unnamed: D4.1 (K), Q4.3
unnamed: D5.2 (A), R7.1
unnamed: D5.1 (K), Q5.3
unnamed: D6.2 (A), R8.1
unnamed: D6.1 (K), Q6.3
unnamed: D9.2 (A), R11.1
unnamed: D9.1 (K), Q9.3
unnamed: D10.2 (A), R12.1
unnamed: D10.1 (K), Q10.3
unnamed: D11.2 (A), R13.1
unnamed: D11.1 (K), Q11.3
unnamed: D12.2 (A), R14.1
unnamed: D12.1 (K), Q12.3
unnamed: D13.2 (A), R15.1
unnamed: D13.1 (K), Q13.3
unnamed: D14.2 (A), R16.1
unnamed: D14.1 (K), Q14.3
unnamed: D15.2 (A), R17.1
unnamed: D15.1 (K), Q15.3
unnamed: D16.2 (A), R18.1
unnamed: D16.1 (K), Q16.3
unnamed: D17.2 (A), R19.1
unnamed: D17.1 (K), Q17.3
unnamed: D18.2 (A), R20.1
unnamed: D18.1 (K), Q18.3
unnamed: D19.2 (A), R21.1
unnamed: D19.1 (K), Q19.3
unnamed: D20.2 (A), R22.1
unnamed: D20.1 (K), Q20.3
unnamed: C4.1, J2.2, R35.1
unnamed: J5.2, R23.1, R38.1
unnamed: J5.3, R24.1, R39.1
unnamed: J6.2, R25.1, R40.1
unnamed: J6.3, R26.1, R41.1
unnamed: J7.2, R27.1, R42.1
unnamed: J7.3, R28.1, R43.1
unnamed: J8.2, R29.1, R44.1
unnamed: J8.3, R30.1, R45.1
unnamed: J9.1, R31.1, R46.1
unnamed: J10.2, R33.1
unnamed: J11.5, R32.1, R47.1
unnamed: Q1.1, R58.2
unnamed: Q2.1, R60.2
unnamed: Q3.1, R62.2
unnamed: Q4.1, R64.2
unnamed: Q5.1, R66.2
unnamed: Q6.1, R68.2
unnamed: Q9.1, R74.2
unnamed: Q10.1, R76.2
unnamed: Q11.1, R78.2
unnamed: Q12.1, R80.2
unnamed: Q13.1, R82.2
unnamed: Q14.1, R84.2
unnamed: Q15.1, R86.2
unnamed: Q16.1, R88.2
unnamed: Q17.1, R90.2
unnamed: Q18.1, R92.2
unnamed: Q19.1, R94.2
unnamed: Q20.1, R96.2
unnamed: R59.1, R61.2
unnamed: R36.2, U1.38 (16_A2_RX4_SCL1)
unnamed: C2.1, U2.5 (CONT)
unnamed: C3.1, R34.1, U7.3 (VOUT)
unnamed: R98.1, U10.11 (LED1+)
unnamed: R99.1, U10.12 (LED2+)
unnamed: R100.1, U10.13 (LED3+)
unnamed: R101.1, U10.14 (LED4+)
unnamed: R102.1, U10.15 (LED5+)
unnamed: R103.1, U10.16 (LED6+)
unnamed: R104.1, U10.17 (LED7+)
unnamed: R105.1, U10.18 (LED8+)
unnamed: R106.1, U10.19 (LED9+)
unnamed: R107.1, U10.20 (LED10+)
SCL: U1.41 (19_A5_SCL), U8.3 (SCL), U11.3 (SCL)
SDA: U1.40 (18_A4_SDA), U8.4 (SDA), U11.4 (SDA)
TORSO: C5.1, J3.2, R36.1
TORSOPANDIR: R92.1, R93.1, U1.6 (4_BCLK2), U9.9 (3A)
TORSOPANDIR5V: J11.3, U9.8 (3Y)
TORSOPANEN: R66.1, U1.5 (3_LRCLK2), U9.2 (1A)
TORSOPANEN5V: J11.1, R49.2, U9.3 (1Y)
TORSOPANPWM: U1.7 (5_IN2), U6.2 (1B), U9.5 (2A*)
TORSOPANPWM5V: R32.2, U9.6 (2Y)
TORSOPANPWMBLINK: R90.1, R91.1, U6.3 (1Y)
TORSOTILT1EN: J7.1, R52.1, R62.1, U1.42 (20_A6_TX5_LRCLK1)
TORSOTILT1LPWM: R28.2, U1.44 (22_A8_CTX1), U4.5 (2B)
TORSOTILT1LPWMBLINK: R84.1, R85.1, U4.6 (2Y)
TORSOTILT1RPWM: R27.2, U1.45 (23_A9_CRX1_MCLK1), U4.2 (1B)
TORSOTILT1RPWMBLINK: R82.1, R83.1, U4.3 (1Y)
TORSOTILT2EN: J8.1, R53.1, R64.1, U1.43 (21_A7_RX5_BCLK1)
TORSOTILT2LPWM: R30.2, U1.20 (28_RX7), U4.13 (4B)
TORSOTILT2LPWMBLINK: R88.1, R89.1, U4.11 (4Y)
TORSOTILT2RPWM: R29.2, U1.21 (29_TX7), U4.10 (3B)
TORSOTILT2RPWMBLINK: R86.1, R87.1, U4.8 (3Y)
V+: J1.1, R59.2
V-: C1.2, C2.2, C3.2, C4.2, C5.2, C9.1, C10.1, J1.2, J2.3, J3.3, J4.2, J9.3, J11.2, J11.4, J11.6, J11.8, Q1.2, Q2.2, Q3.2, Q4.2, Q5.2, Q6.2, Q9.2, Q10.2, Q11.2, Q12.2, Q13.2, Q14.2, Q15.2, Q16.2, Q17.2, Q18.2, Q19.2, Q20.2, R38.2, R39.2, R40.2, R41.2, R42.2, R43.2, R44.2, R45.2, R46.2, R47.2, R48.2, R49.1, R50.2, R51.2, R52.2, R53.2, R63.2, R75.2, R77.2, R79.2, R81.2, R83.2, R85.2, R87.2, R89.2, R91.2, R93.2, R95.2, R97.2, U1.1 (GND), U1.34 (GND), U1.47 (GND), U1.52 (GND), U2.1 (GND), U3.7 (GND), U4.7 (GND), U5.1 (1OE*), U5.4 (2OE*), U5.7 (GND), U5.10 (3OE*), U5.13 (4OE*), U6.7 (GND), U7.2 (GND), U8.2 (GND), U9.1 (1OE*), U9.4 (2OE*), U9.7 (GND), U9.10 (3OE*), U10.1 (LED1-), U10.2 (LED2-), U10.3 (LED3-), U10.4 (LED4-), U10.5 (LED5-), U10.6 (LED6-), U10.7 (LED7-), U10.8 (LED8-), U10.9 (LED9-), U10.10 (LED10-), U11.2 (GND)
VSENSE: C10.2, R65.1, U1.39 (17_A3_TX4_SDA1)

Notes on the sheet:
HEAD TILT ACTUATORS
TORSO PAN
HEAD PAN DIR
Gates
Battery Charge Meter
TORSO TILT 1 RPWM
HEAD TILT 2
TORSO TILT 2
HEAD TILT 1
TORSO PAN PWM
TORSO PAN DIR
Sensors
Motors
Mount Holes
TORSO TILT 1 LPWM
Level Shifters 3.3V to 5V
555 Timer
Controller
Voltage Sensing
HEAD TILT 1 RPWM
TORSO TILT ACTUATORS
FULL
Activity Indicators (Blue)
TORSO TILT 1
Voltage / Current Meter OLED Display
TORSO VELOCITY CONTROL SERVO
HEAD PAN
Status Indicators (Red)
Servos
HEAD TILT POTENTIOMETER
Current Sensing
EMPTY
SIDE WITH PART NUMBER PRINTED
HEAD TILT 2 LPWM
Servo Power 7.5V
TORSO TILT 2 LPWM
TORSO TILT POTENTIOMETER
MOUTH POSITION CONTROL SERVO
HEAD STEPPER
HEAD TILT 1 LPWM

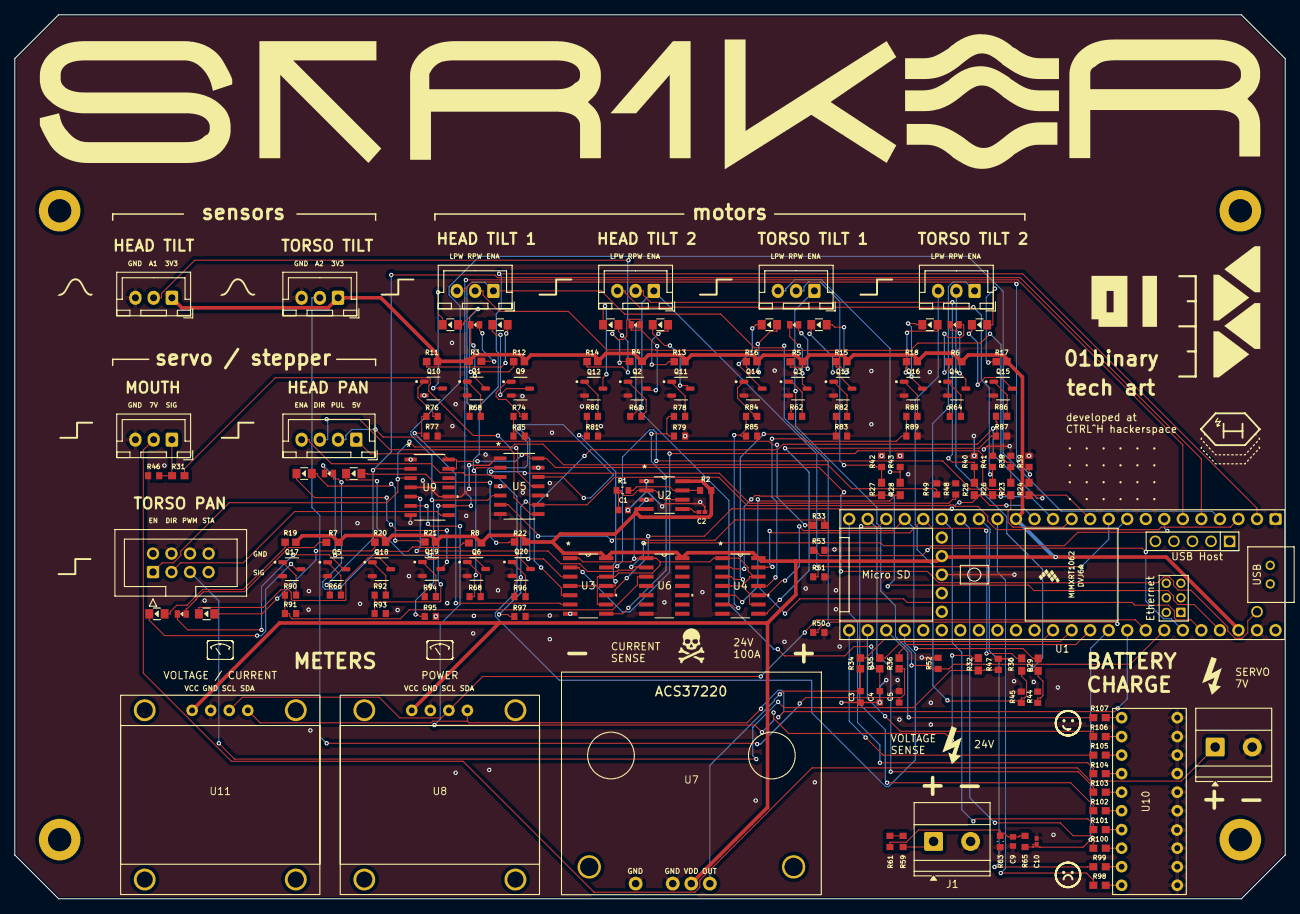
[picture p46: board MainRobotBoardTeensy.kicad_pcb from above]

Board: 2 copper layers, 174.0 x 121.1 mm, 163 parts (0 on the bottom side), 140 nets.

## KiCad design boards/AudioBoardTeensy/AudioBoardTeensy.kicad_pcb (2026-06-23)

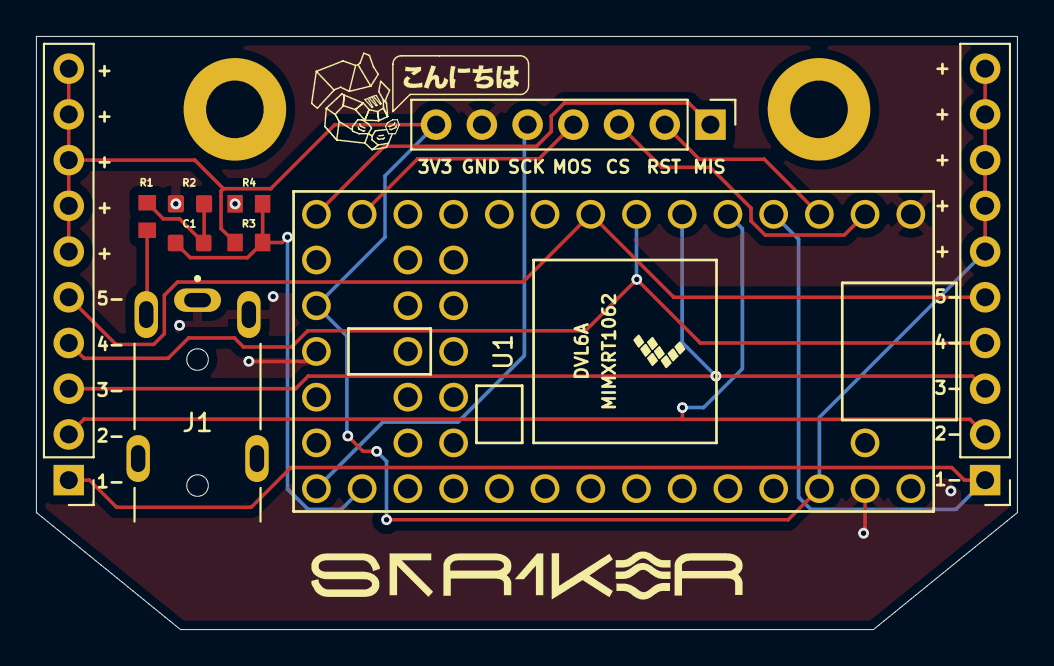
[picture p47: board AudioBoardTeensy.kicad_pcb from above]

Board: 2 copper layers, 54.5 x 33.0 mm, 12 parts (0 on the bottom side), 15 nets.

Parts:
C1: 10uF; CL10A106KP8NNNC
H1, H2: MountingHole_Pad; MountingHole_3.2mm_M3_ISO7380_Pad
J1: 54-00174
J2, J3: Conn_01x10_Pin; PinHeader_1x10_P2.54mm_Vertical
J4: DFR0934; PinHeader_1x07_P2.54mm_Vertical
R1: 1K; RCG06031K00FKEA
R2: 2K; 0603WAF2001T5E
R3, R4: 100K; CRCW0603100KFKEA
U1: Teensy4.0; Teensy40

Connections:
+3V3: J2.6, J2.7, J2.8, J2.9, J2.10, J3.6, J3.7, J3.8, J3.9, J3.10, J4.7, R3.2, U1.16 (3V3), U1.31 (3V3)
A0: C1.1, R3.1, R4.2, U1.21 (14_A0_TX3_SPDIF_OUT)
AUDIO: J1.2, R1.2
CS: J4.3, U1.2 (0_RX1_CRX2_CS1)
GND: J1.1, J1.3, J4.6, R2.1, R4.1, U1.1 (GND), U1.17 (GND), U1.32 (GND)
LED1: J2.1, J3.1, U1.4 (2_OUT2)
LED2: J2.2, J3.2, U1.5 (3_LRCLK2)
LED3: J2.3, J3.3, U1.6 (4_BCLK2)
LED4: J2.4, J3.4, U1.7 (5_IN2)
LED5: J2.5, J3.5, U1.8 (6_OUT1D)
MISO: J4.1, U1.14 (12_MISO_MQSL)
MOSI: J4.4, U1.13 (11_MOSI_CTX1)
unnamed: C1.2, R1.1, R2.2
RST: J4.2, U1.3 (1_TX1_CTX2_MISO1)
SCK: J4.5, U1.20 (13_SCK_CRX1_LED)

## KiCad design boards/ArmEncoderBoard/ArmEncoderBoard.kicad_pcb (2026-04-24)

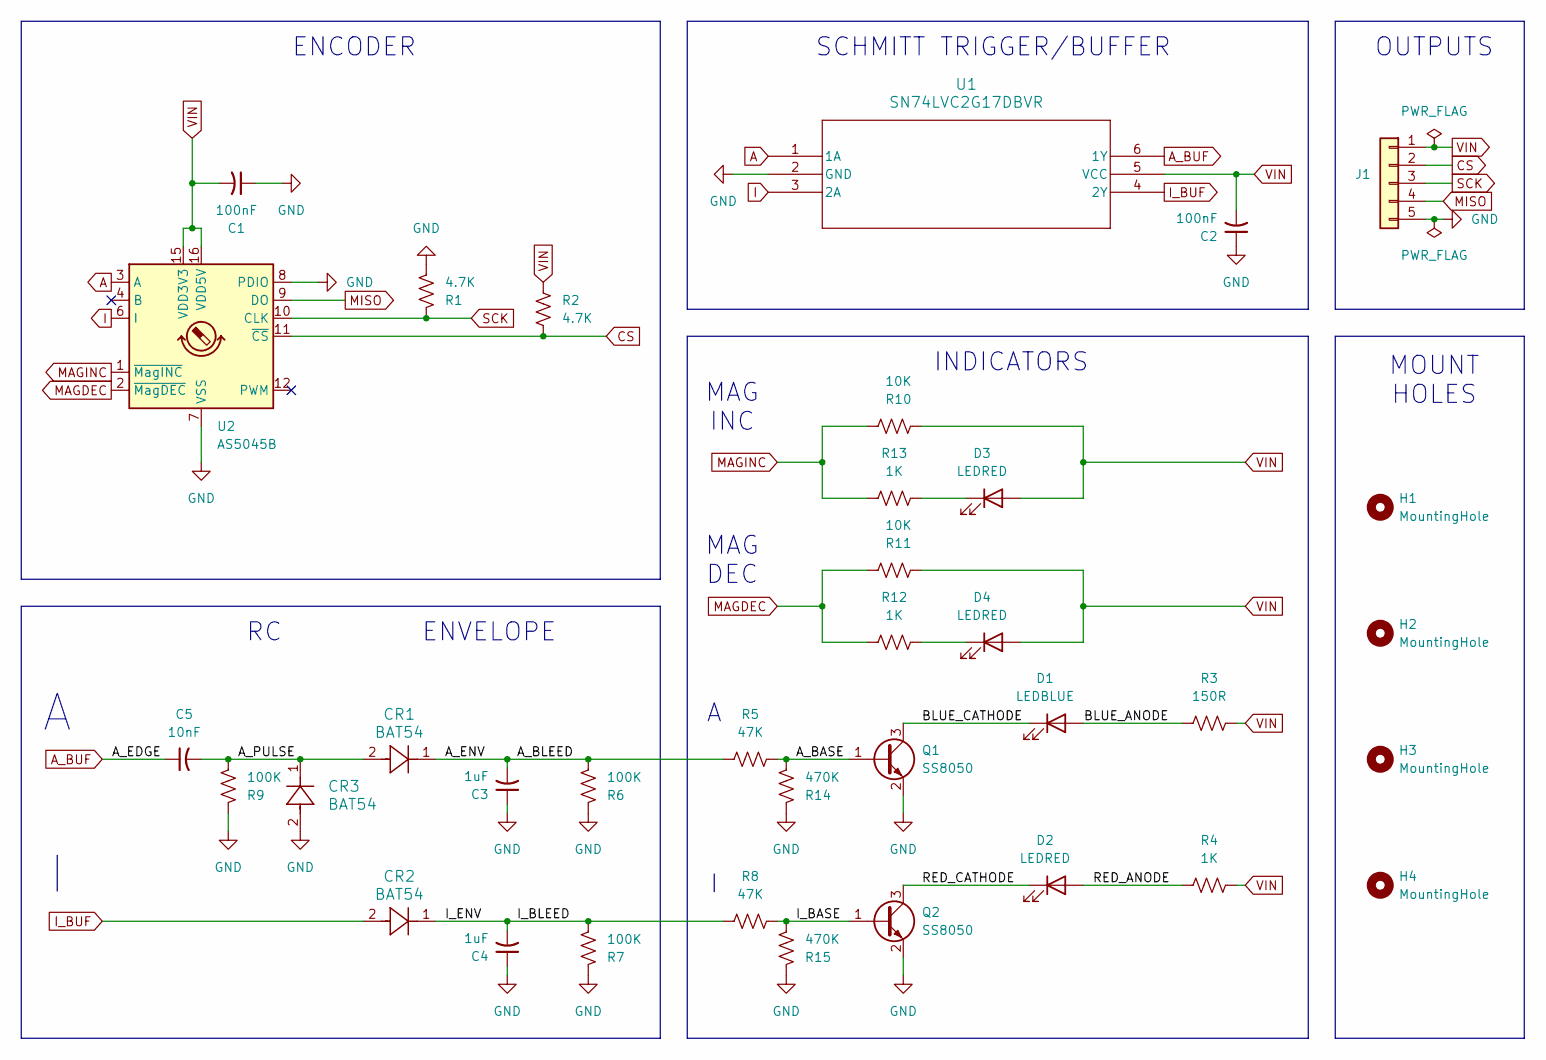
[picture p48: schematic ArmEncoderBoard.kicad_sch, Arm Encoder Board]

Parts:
C1, C2: 100nF; CC0603KRX7R9BB104; LCSC C14663
C3, C4: 1uF; CC0603JRX7R7BB105-L; LCSC C519560
C5: 10nF; GRM1885C1H103JA01D; LCSC C85973
CR1, CR2, CR3: BAT54; BAT54WS-7-F; LCSC C124205
D1: LEDBLUE; 150080BS75000_Modified; LCSC C6067133
D2, D3, D4: LEDRED; NCD0603R1; LCSC C84263
H1, H2, H3, H4: MountingHole; MountingHole_3.5mm_Pad
J1: Conn_01x05; JST_XH_B5B-XH-A_1x05_P2.50mm_Vertical
Q1, Q2: SS8050; SOT-23; LCSC C81464
R1, R2: 4.7K; CR0603-FX-4701ELF; LCSC C840629
R3: 150R; RESC1607X60N; LCSC C114608
R4, R12, R13: 1K; RCG06031K00FKEA; LCSC C4264491
R5, R8: 47K; RC0603FR-0747KL; LCSC C105579
R6, R7, R9: 100K; CRCW0603100KFKEA; LCSC C844916
R10, R11: 10K; CRCW060310K0FKEA; LCSC C95204
R14, R15: 470K; RC0603FR-07470KL; LCSC C114622
U1: SN74LVC2G17DBVR; LCSC C10429
U2: AS5045B; SSOP-16_5.3x6.2mm_P0.65mm; LCSC C5375289

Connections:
/A_BASE: Q1.1 (B), R5.1, R14.2
/A_ENV: C3.2, CR1.1, R5.2, R6.2
/A_PULSE: C5.2, CR1.2, CR3.1, R9.2
/BLUE_ANODE: D1.2 (A), R3.2
/BLUE_CATHODE: D1.1 (K), Q1.3 (C)
/I_BASE: Q2.1 (B), R8.1, R15.2
/I_ENV: C4.2, CR2.1, R7.2, R8.2
/RED_ANODE: D2.2 (A), R4.2
/RED_CATHODE: D2.1 (K), Q2.3 (C)
A: U1.1 (1A), U2.3 (A)
A_BUF: C5.1, U1.6 (1Y)
CS: J1.2, R2.2, U2.11 (~CS)
GND: C1.1, C2.1, C3.1, C4.1, CR3.2, J1.5, Q1.2 (E), Q2.2 (E), R1.2, R6.1, R7.1, R9.1, R14.1, R15.1, U1.2 (GND), U2.7 (VSS), U2.8 (PDIO)
I: U1.3 (2A), U2.6 (I)
I_BUF: CR2.2, U1.4 (2Y)
MAGDEC: R11.2, R12.2, U2.2 (~MagDEC)
MAGINC: R10.2, R13.2, U2.1 (~MagINC)
MISO: J1.4, U2.9 (DO)
unnamed: D3.1 (K), R13.1
unnamed: D4.1 (K), R12.1
SCK: J1.3, R1.1, U2.10 (CLK)
VIN: C1.2, C2.2, D3.2 (A), D4.2 (A), J1.1, R2.1, R3.1, R4.1, R10.1, R11.1, U1.5 (VCC), U2.15 (VDD3V3), U2.16 (VDD5V)

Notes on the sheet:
ENVELOPE
MOUNT HOLES
INDICATORS
MAG DEC
SCHMITT TRIGGER/BUFFER
ENCODER
MAG INC
OUTPUTS

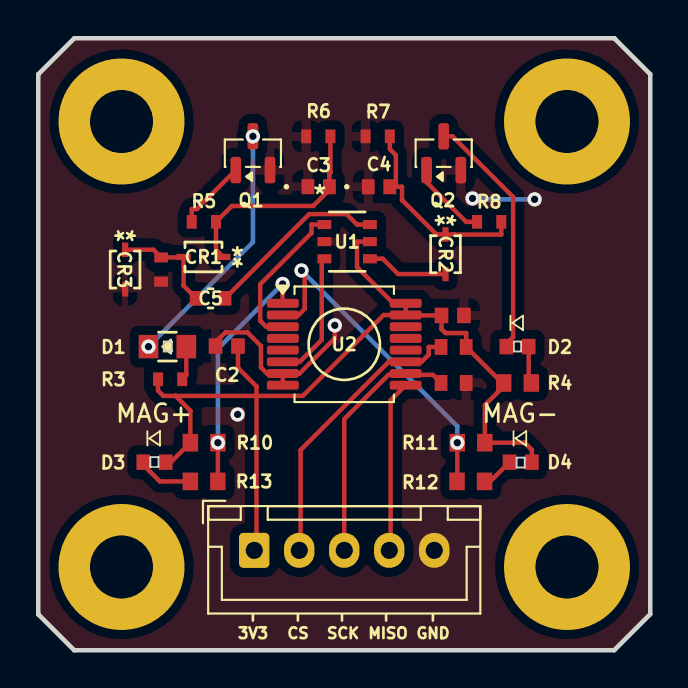
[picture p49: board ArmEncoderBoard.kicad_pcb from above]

Board: 2 copper layers, 34.0 x 34.0 mm, 34 parts (0 on the bottom side), 22 nets.

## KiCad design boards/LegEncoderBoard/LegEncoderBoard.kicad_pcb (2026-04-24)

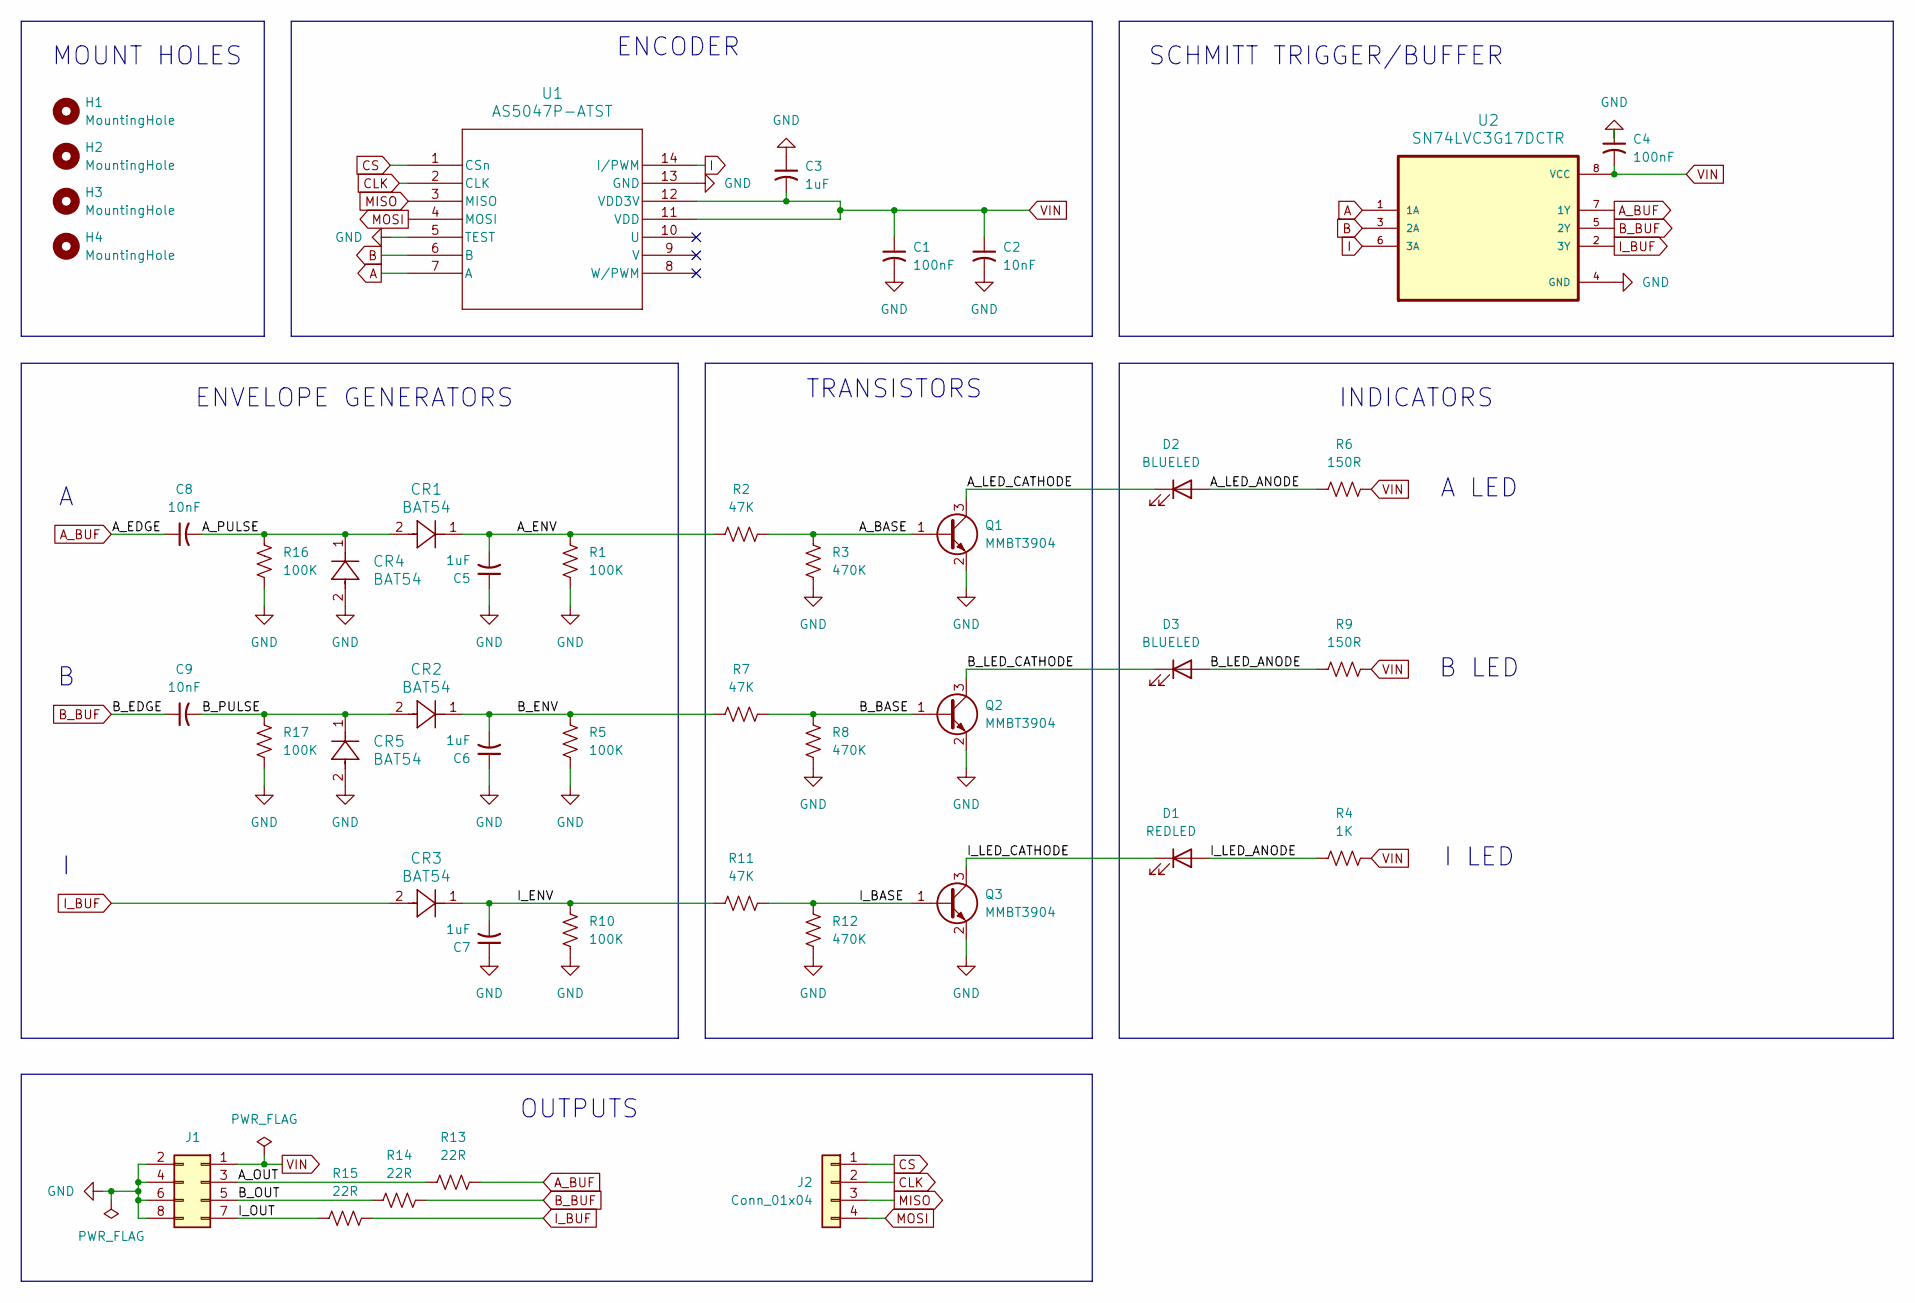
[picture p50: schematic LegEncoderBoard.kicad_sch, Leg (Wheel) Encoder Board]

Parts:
C1, C4: 100nF; CC0603KRX7R9BB104; LCSC C14663
C2, C8, C9: 10nF; GRM1885C1H103JA01D; LCSC C85973
C3, C5, C6, C7: 1uF; CC0603JRX7R7BB105; LCSC C519560
CR1, CR2, CR3, CR4, CR5: BAT54; BAT54WS-7-F; LCSC C124205
D1: REDLED; NCD0603R1; LCSC C114608
D2, D3: BLUELED; 150080BS75000_Modified; LCSC C6067133
H1, H2, H3, H4: MountingHole; MountingHole_2.5mm_Pad
J1: Conn_01x05; IDC-Header_2x04_P2.54mm_Vertical
J2: Conn_01x04; JST_XH_B4B-XH-A_1x04_P2.50mm_Vertical
Q1, Q2, Q3: MMBT3904; MMBT3904LT1G; LCSC C81464
R1, R5, R10, R16, R17: 100K; CRCW0603100KFKEA; LCSC C844916
R2, R7, R11: 47K; RC0603FR-0747KL; LCSC C105579
R3, R8, R12: 470K; RC0603FR-07470KL; LCSC C114622
R4: 1K; RCG06031K00FKEA; LCSC C4264491
R6, R9: 150R; RESC1607X60N; LCSC C114608
R13, R14, R15: 22R; RC0603FR-0722RL; LCSC C107701
U1: AS5047P-ATST; AS5047P-ASST; LCSC C962063
U2: SN74LVC3G17DCTR; PARTREV F; LCSC C18213

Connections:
/A_BASE: Q1.1 (B), R2.2, R3.1
/A_ENV: C5.2, CR1.1, R1.1, R2.1
/A_LED_ANODE: D2.2 (A), R6.2
/A_LED_CATHODE: D2.1 (K), Q1.3 (C)
/A_OUT: J1.3, R13.1
/A_PULSE: C8.2, CR1.2, CR4.1, R16.1
/B_BASE: Q2.1 (B), R7.2, R8.1
/B_ENV: C6.2, CR2.1, R5.1, R7.1
/B_LED_ANODE: D3.2 (A), R9.2
/B_LED_CATHODE: D3.1 (K), Q2.3 (C)
/B_OUT: J1.5, R14.1
/B_PULSE: C9.2, CR2.2, CR5.1, R17.1
/I_BASE: Q3.1 (B), R11.2, R12.1
/I_ENV: C7.2, CR3.1, R10.1, R11.1
/I_LED_ANODE: D1.2 (A), R4.2
/I_LED_CATHODE: D1.1 (K), Q3.3 (C)
/I_OUT: J1.7, R15.1
A: U1.7 (A), U2.1 (1A)
A_BUF: C8.1, R13.2, U2.7 (1Y)
B: U1.6 (B), U2.3 (2A)
B_BUF: C9.1, R14.2, U2.5 (2Y)
CLK: J2.2, U1.2 (CLK)
CS: J2.1, U1.1 (CSn)
GND: C1.2, C2.2, C3.1, C4.1, C5.1, C6.1, C7.1, CR4.2, CR5.2, J1.2, J1.4, J1.6, J1.8, Q1.2 (E), Q2.2 (E), Q3.2 (E), R1.2, R3.2, R5.2, R8.2, R10.2, R12.2, R16.2, R17.2, U1.5 (TEST), U1.13 (GND), U2.4 (GND)
I: U1.14 (I/PWM), U2.6 (3A)
I_BUF: CR3.2, R15.2, U2.2 (3Y)
MISO: J2.3, U1.3 (MISO)
MOSI: J2.4, U1.4 (MOSI)
VIN: C1.1, C2.1, C3.2, C4.2, J1.1, R4.1, R6.1, R9.1, U1.11 (VDD), U1.12 (VDD3V), U2.8 (VCC)

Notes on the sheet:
ENVELOPE GENERATORS
ENCODER
I LED
B LED
INDICATORS
OUTPUTS
A LED
MOUNT HOLES
TRANSISTORS
SCHMITT TRIGGER/BUFFER

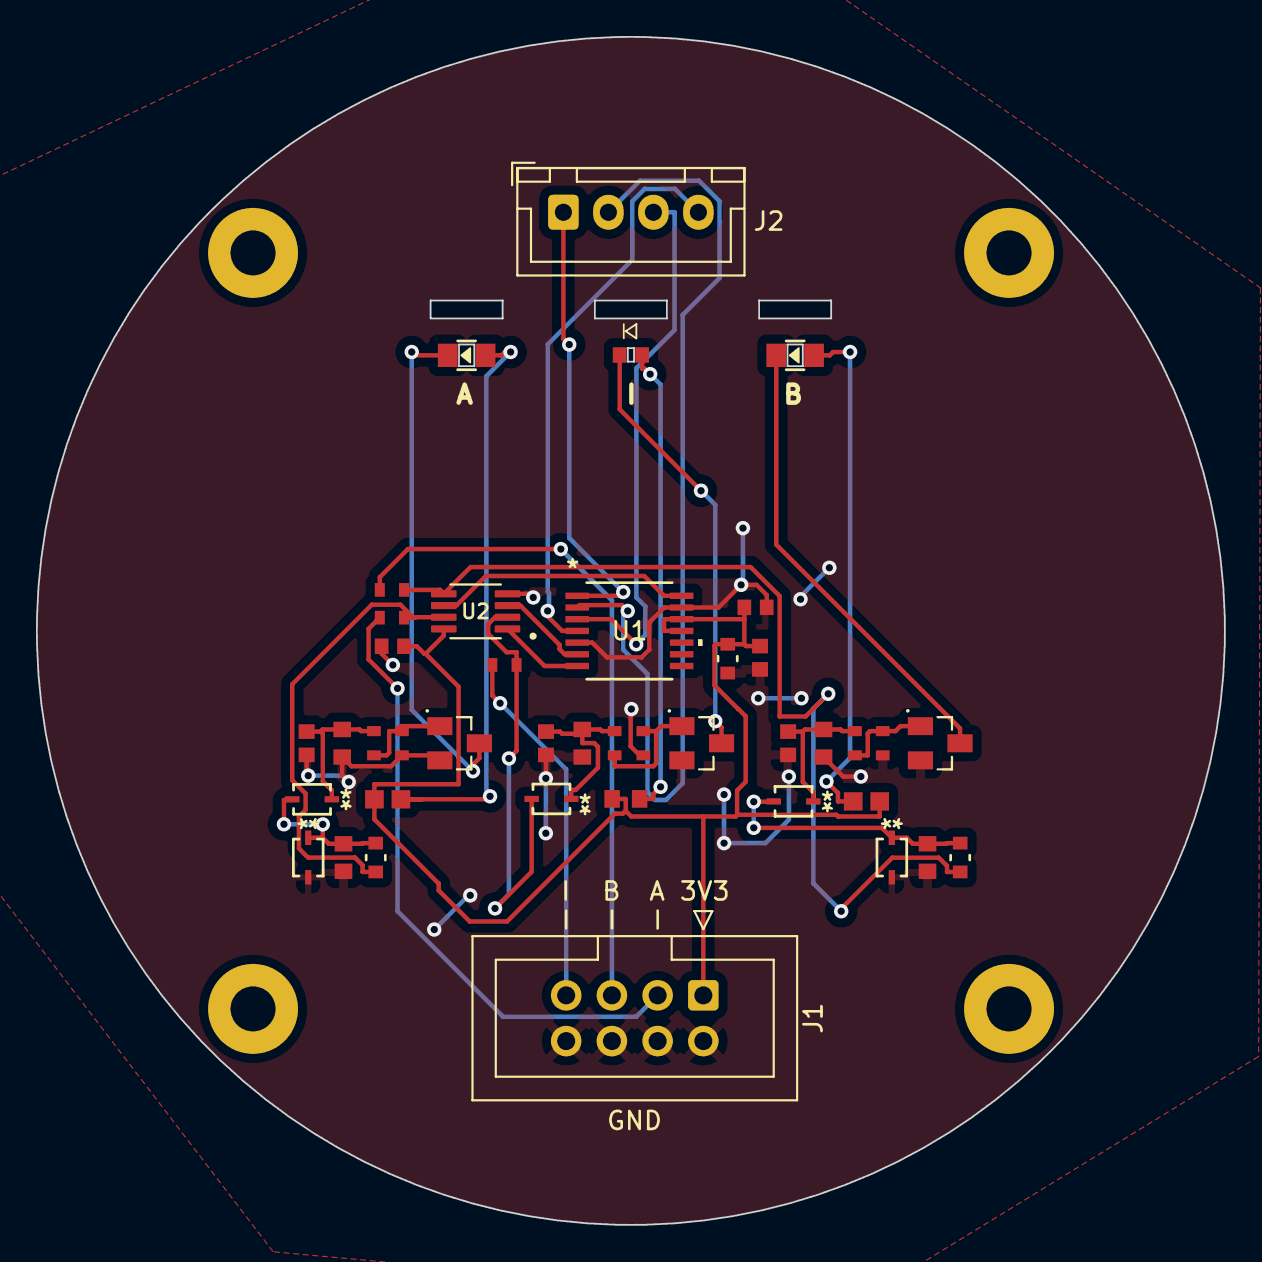
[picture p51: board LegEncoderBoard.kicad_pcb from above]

Board: 2 copper layers, 66.0 x 66.0 mm, 45 parts (0 on the bottom side), 29 nets.

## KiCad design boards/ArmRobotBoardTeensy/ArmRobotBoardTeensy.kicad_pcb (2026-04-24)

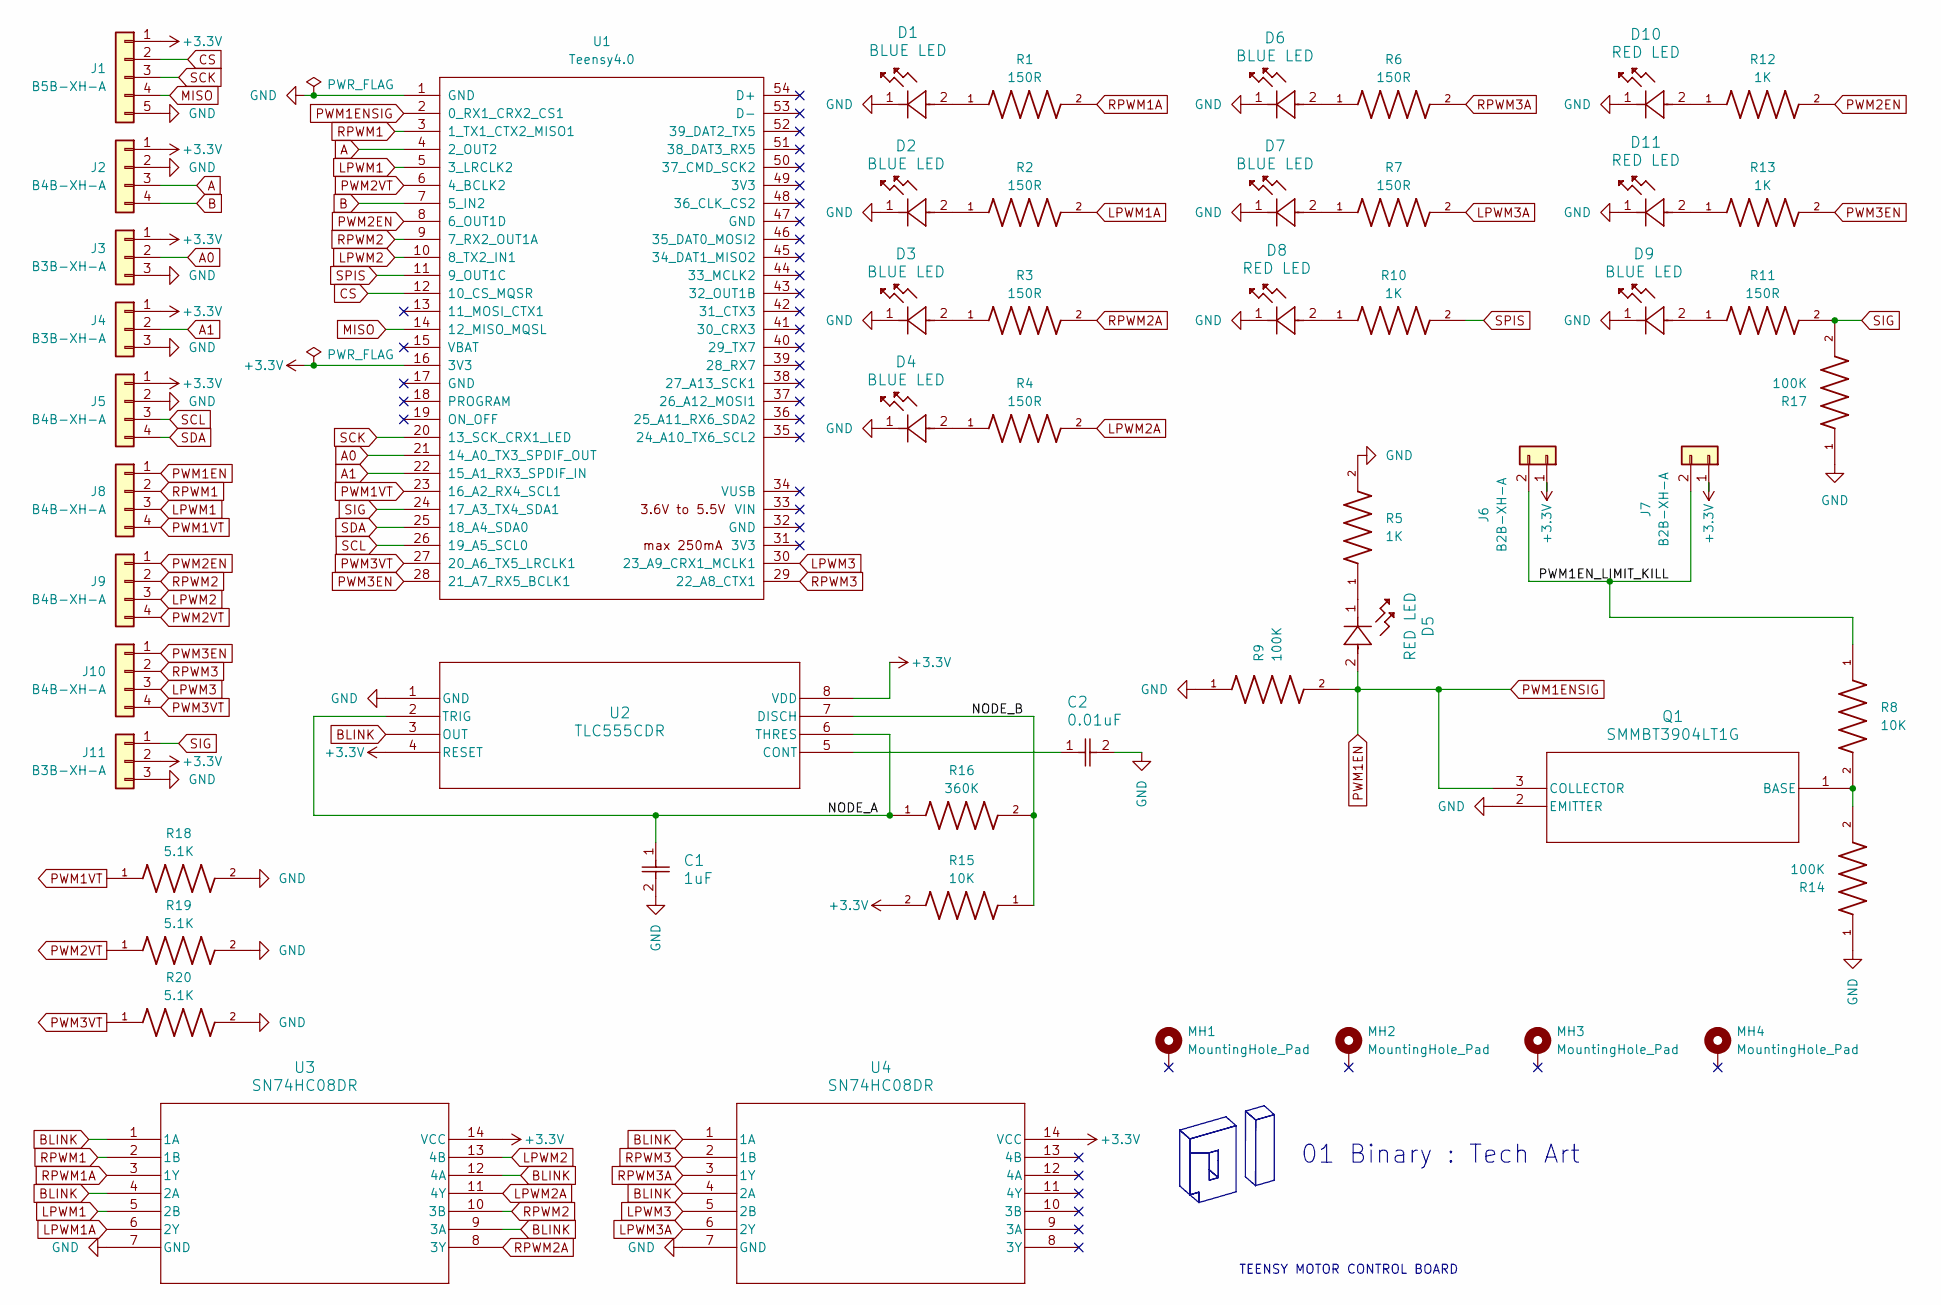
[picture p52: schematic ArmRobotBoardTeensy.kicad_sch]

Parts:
C1: 1uF; CC0603JRX7R7BB105; LCSC C519560
C2: 0.01uF; C0402C103J4RACTU; LCSC C2167451
D1, D2, D3, D4, D6, D7, D9: BLUE LED; 150080BS75000_Modified; LCSC C6067133
D5, D8, D10, D11: RED LED; NCD0603R1; LCSC C84263
J1: B5B-XH-A; JST_XH_B5B-XH-A_1x05_P2.50mm_Vertical
J2, J5, J8, J9, J10: B4B-XH-A; JST_XH_B4B-XH-A_1x04_P2.50mm_Vertical
J3, J4, J11: B3B-XH-A; JST_XH_B3B-XH-A_1x03_P2.50mm_Vertical
J6, J7: B2B-XH-A; JST_XH_B2B-XH-A_1x02_P2.50mm_Vertical
MH1, MH2, MH3, MH4: MountingHole_Pad; MountingHole_3.2mm_M3_ISO7380_Pad
Q1: SMMBT3904LT1G; LCSC C84555
R1, R2, R3, R4, R6, R7, R11: 150R; RCG06031K00FKEA; LCSC C114608
R5, R10, R12, R13: 1K; RCG06031K00FKEA; LCSC C4264491
R8, R15: 10K; CRCW060310K0FKEA; LCSC C844918
R9, R14, R17: 100K; CRCW0603100KFKEA; LCSC C844916
R16: 360K; RC0603FR-07360KL; LCSC C137740
R18, R19, R20: 5.1K; RC0603FR-075K1L; LCSC C105580
U1: Teensy4.0; Teensy40_SMT
U2: TLC555CDR; LCSC C6986
U3, U4: SN74HC08DR; LCSC C337768

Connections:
+3.3V: J1.1, J2.1, J3.1, J4.1, J5.1, J6.1, J7.1, J11.2, R15.2, U1.16 (3V3), U2.4 (RESET), U2.8 (VDD), U3.14 (VCC), U4.14 (VCC)
/NODE_A: C1.1, R16.1, U2.2 (TRIG), U2.6 (THRES)
/NODE_B: R15.1, R16.2, U2.7 (DISCH)
/PWM1EN_LIMIT_KILL: J6.2, J7.2, R8.1
A: J2.3, U1.4 (2_OUT2)
A0: J3.2, U1.21 (14_A0_TX3_SPDIF_OUT)
A1: J4.2, U1.22 (15_A1_RX3_SPDIF_IN)
B: J2.4, U1.7 (5_IN2)
BLINK: U2.3 (OUT), U3.1 (1A), U3.4 (2A), U3.9 (3A), U3.12 (4A), U4.1 (1A), U4.4 (2A)
CS: J1.2, U1.12 (10_CS_MQSR)
GND: C1.2, C2.2, D1.1, D2.1, D3.1, D4.1, D6.1, D7.1, D8.1, D9.1, D10.1, D11.1, J1.5, J2.2, J3.3, J4.3, J5.2, J11.3, Q1.2 (EMITTER), R5.2, R9.1, R14.1, R17.1, R18.2, R19.2, R20.2, U1.1 (GND), U2.1 (GND), U3.7 (GND), U4.7 (GND)
LPWM1: J8.3, U1.5 (3_LRCLK2), U3.5 (2B)
LPWM1A: R2.2, U3.6 (2Y)
LPWM2: J9.3, U1.10 (8_TX2_IN1), U3.13 (4B)
LPWM2A: R4.2, U3.11 (4Y)
LPWM3: J10.3, U1.30 (23_A9_CRX1_MCLK1), U4.5 (2B)
LPWM3A: R7.2, U4.6 (2Y)
MISO: J1.4, U1.14 (12_MISO_MQSL)
unnamed: D1.2, R1.1
unnamed: D2.2, R2.1
unnamed: D3.2, R3.1
unnamed: D4.2, R4.1
unnamed: D5.1, R5.1
unnamed: D6.2, R6.1
unnamed: D7.2, R7.1
unnamed: D8.2, R10.1
unnamed: D9.2, R11.1
unnamed: D10.2, R12.1
unnamed: D11.2, R13.1
unnamed: Q1.1 (BASE), R8.2, R14.2
unnamed: C2.1, U2.5 (CONT)
PWM1EN: D5.2, J8.1, Q1.3 (COLLECTOR), R9.2, U1.2 (0_RX1_CRX2_CS1)
PWM1VT: J8.4, R18.1, U1.23 (16_A2_RX4_SCL1)
PWM2EN: J9.1, R12.2, U1.8 (6_OUT1D)
PWM2VT: J9.4, R19.1, U1.6 (4_BCLK2)
PWM3EN: J10.1, R13.2, U1.28 (21_A7_RX5_BCLK1)
PWM3VT: J10.4, R20.1, U1.27 (20_A6_TX5_LRCLK1)
RPWM1: J8.2, U1.3 (1_TX1_CTX2_MISO1), U3.2 (1B)
RPWM1A: R1.2, U3.3 (1Y)
RPWM2: J9.2, U1.9 (7_RX2_OUT1A), U3.10 (3B)
RPWM2A: R3.2, U3.8 (3Y)
RPWM3: J10.2, U1.29 (22_A8_CTX1), U4.2 (1B)
RPWM3A: R6.2, U4.3 (1Y)
SCK: J1.3, U1.20 (13_SCK_CRX1_LED)
SCL: J5.3, U1.26 (19_A5_SCL0)
SDA: J5.4, U1.25 (18_A4_SDA0)
SIG: J11.1, R11.2, R17.2, U1.24 (17_A3_TX4_SDA1)
SPIS: R10.2, U1.11 (9_OUT1C)

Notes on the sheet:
TEENSY MOTOR CONTROL BOARD
01 Binary : Tech Art


Board: 2 copper layers, 87.5 x 55.0 mm, 53 parts (0 on the bottom side), 48 nets.

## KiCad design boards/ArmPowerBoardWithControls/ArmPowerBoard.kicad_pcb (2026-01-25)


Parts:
J1, J2, J3, J4, J5: XT60PW-F; XT-60-Measured
LED1, LED2, LED3, LED4, LED5: 3V 20mA; LED_D3.0mm
SW1, SW2, SW3, SW4: ExternalSwitch

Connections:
GND: J1.2, J2.2, J3.2, J4.2, J5.2, LED1.1 (K), LED2.1 (K), LED3.1 (K), LED4.1 (K), LED5.1 (K)
unnamed: J1.1, LED1.2 (A), SW1.2 (B)
unnamed: J2.1, LED2.2 (A), SW2.2 (B)
unnamed: J3.1, LED3.2 (A), SW3.2 (B)
unnamed: J4.1, LED4.2 (A), SW4.2 (B)
unnamed: J5.1, LED5.2 (A), SW1.1 (A), SW2.1 (A), SW3.1 (A), SW4.1 (A)


Board: 2 copper layers, 58.4 x 46.5 mm, 14 parts (0 on the bottom side), 6 nets.

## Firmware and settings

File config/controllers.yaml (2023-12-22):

robot:
  rate: 50
  arm1:
    controller: 'arm'
    base:
      actuator:
        controller: 'motor'
        topic: 'pwm'
        lpwm: 0
        rpwm: 1
        minPwm: 64
        maxPwm: 255
        minVelocity: 0.0
        maxVelocity: 1.0
        pid:
          p: 0.4079
          i: 0.05242
          d: 0.1964
          i_clamp: 1.0
      encoder:
        controller: 'encoder'
        topic: 'adc'
        channel: 0
        minReading: 810
        maxReading: 258
        minPos: -1.4929
        maxPos: 1.4929
        threshold: 8
        average: 2
    upperarm_actuator:
      actuator:
        controller: 'motor'
        topic: 'pwm'
        lpwm: 2
        rpwm: 3
        minPwm: 32
        maxPwm: 255
        minVelocity: 0.0
        maxVelocity: 1.0
        pid:
          p: 3.149
          i: 4.687
          d: 0.03102
          i_clamp: 1.0
      encoder:
        controller: 'encoder'
        topic: 'adc'
        channel: 1
        minReading: 857
        maxReading: 902
        minPos: -0.054
        maxPos: -0.0005
        threshold: 8
        average: 2
    forearm_actuator:
      actuator:
        controller: 'motor'
        topic: 'pwm'
        lpwm: 4
        rpwm: 5
        minPwm: 200
        maxPwm: 255
        minVelocity: 0.0
        maxVelocity: 1.0
        pid:
          p: 31.12
          i: 10.22
          d: 0.3102
          i_clamp: 1.0
      encoder:
        controller: 'encoder'
        topic: 'adc'
        channel: 6
        minReading: 976
        maxReading: 848
        minPos: -0.0508
        maxPos: 0
        threshold: 8
        average: 8
    wrist:
      actuator:
        controller: 'solenoid'
        topic: 'pwm'
        channel: 6
        triggerSeconds: 0.023

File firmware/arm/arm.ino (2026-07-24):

/*
                                                                                     ███████                  
 ████████████  ████████████   ████████████       █  █████████████  █           █  ███       ███  ████████████ 
█              █ █           █            █    █ █  █              █        ███      ███████    █            █
 ████████████  █   █         █████████████   █   █   █             █   █████      ███       ███ █████████████ 
             █ █     █       █            █      █    █            ████      █                  █            █
 ████████████  █       █     █            █      █      █████████  █          █   ███       ███ █            █
                                                                                     ███████                  
 arm.ino
 Arm Motor Control Board Firmware
 Copyright (C) 2026 Valeriy Novytskyy
 This software is licensed under GNU GPLv3
*/

/*----------------------------------------------------------*\
| Includes
\*----------------------------------------------------------*/

#include <ros.h>                        // See ../../../readme.md
#include <ros/time.h>                   // ROS time tracking
#include <str1ker/VelocityCommand.h>    // Velocity message
#include <str1ker/PositionCommand.h>    // Position message
#include <str1ker/GripperCommand.h>     // Gripper message
#include <str1ker/StateFeedback.h>      // State message
#include <str1ker/RawStateFeedback.h>   // Raw state message
#include <firmware.h>                   // See ../readme.md

/*----------------------------------------------------------*\
| Constants
\*----------------------------------------------------------*/

const int RATE_HZ = 50;                 // Default real time update rate
const int STARTUP_DELAY = 3000;         // Prevent "published too soon" errors

const int BASE_EN = 0;                  // Base motor driver Enabled pin
const int BASE_RPWM = 1;                // Base motor driver right PWM pin
const int BASE_LPWM = 3;                // Base motor driver left PWM pin
const int BASE_SENSE = A2;              // Base motor driver current sense pin
const int BASE_A = 2;                   // Base quadrature encoder A pin
const int BASE_B = 5;                   // Base quadrature encoder B pin
const int BASE_CS = 10;                 // Base absolute encoder chip select pin
const int BASE_SCK = 13;                // Base absolute encoder clock pin
const int BASE_MISO = 12;               // Base absolute encoder data pin
const int BASE_STATUS = 9;              // Base absolute encoder status pin

const int SHOULDER_EN = 6;              // Shoulder motor driver Enabled pin
const int SHOULDER_RPWM = 7;            // Shoulder motor driver right PWM pin
const int SHOULDER_LPWM = 8;            // Shoulder motor driver left PWM pin
const int SHOULDER_SENSE = 4;           // Shoulder motor driver current sense pin
const int SHOULDER_POTENTIOMETER = A0;  // Shoulder potentiometer pin

const int ELBOW_EN = 21;                // Elbow motor driver Enabled pin
const int ELBOW_RPWM = 22;              // Elbow motor right PWM pin
const int ELBOW_LPWM = 23;              // Elbow motor left PWM pin
const int ELBOW_SENSE = 20;             // Elbow motor current sense pin
const int ELBOW_POTENTIOMETER = A1;     // Elbow motor potentiometer pin

const int GRIPPER_PIN = 17;             // Gripper solenoid pin

/*----------------------------------------------------------*\
| Definitions
\*----------------------------------------------------------*/

typedef ros::Subscriber<str1ker::VelocityCommand> VelocitySubscriber;
typedef ros::Subscriber<str1ker::PositionCommand> PositionSubscriber;
typedef ros::Subscriber<str1ker::GripperCommand> GripperSubscriber;

/*----------------------------------------------------------*\
| Declarations
\*----------------------------------------------------------*/

ros::NodeHandle& initializeRos();
void initializeRosInterface();
void initializeJoints();
void loadSettings();
void updateJoints(float timeStep);
void velocityCommand(const str1ker::VelocityCommand& msg);
void positionCommand(const str1ker::PositionCommand& msg);
void gripperCommand(const str1ker::GripperCommand& msg);
void stateFeedback();
void rawFeedback();

/*----------------------------------------------------------*\
| Variables
\*----------------------------------------------------------*/

ros::NodeHandle node;
str1ker::StateFeedback stateFeedbackMsg;
str1ker::RawStateFeedback rawFeedbackMsg;
ros::Publisher statePub("arm1/state", &stateFeedbackMsg);
ros::Publisher rawPub("arm1/raw", &rawFeedbackMsg);
VelocitySubscriber velocitySub("arm1/velocity", velocityCommand);
PositionSubscriber positionSub("arm1/position", positionCommand);
GripperSubscriber gripperSub("arm1/gripper", gripperCommand);
Actuator<AbsoluteEncoder, Motor> baseJoint("base");
Actuator<Potentiometer, Motor> shoulderJoint("shoulder");
Actuator<Potentiometer, Motor> elbowJoint("elbow");
Solenoid gripper;
VoltageCurrentSensor supplySensor;
bool debug;

/*----------------------------------------------------------*\
| Entry points
\*----------------------------------------------------------*/

void setup()
{
  initializeRos();
  initializeJoints();
  supplySensor.initialize();
  loadSettings();
  initializeRosInterface();

  delay(STARTUP_DELAY);
}

void loop()
{
  static uint32_t last = 0;

  uint32_t now = millis();
  const uint32_t period = 1000 / RATE_HZ;

  if (last == 0)
  {
    last = now;
    node.spinOnce();
    return;
  }

  if (now < STARTUP_DELAY)
  {
    last = now;
    node.spinOnce();
    return;
  }

  uint32_t elapsed = now - last;

  if (elapsed < period)
  {
    node.spinOnce();
    return;
  }

  float timeStep = elapsed * 0.001f;

  if (timeStep <= 0.0f)
  {
    node.spinOnce();
    return;
  }

  updateJoints(timeStep);

  node.spinOnce();
  last = now;
}

/*----------------------------------------------------------*\
| Functions
\*----------------------------------------------------------*/

ros::NodeHandle& initializeRos()
{
  node.initNode();

  while (!node.connected())
  {
    node.spinOnce();
    delay(10);
  }

  return node;
}

void initializeRosInterface()
{
  node.advertise(statePub);

  if (debug)
  {
    node.advertise(rawPub);
  }

  node.subscribe(velocitySub);
  node.subscribe(positionSub);
  node.subscribe(gripperSub);
  node.negotiateTopics();
}

void initializeJoints()
{
  baseJoint.motor.initialize(BASE_EN, BASE_LPWM, BASE_RPWM, BASE_SENSE);
  baseJoint.encoder.initialize(BASE_STATUS, BASE_CS);

  shoulderJoint.motor.initialize(SHOULDER_EN, SHOULDER_LPWM, SHOULDER_RPWM, SHOULDER_SENSE);
  shoulderJoint.encoder.initialize(SHOULDER_POTENTIOMETER);

  elbowJoint.motor.initialize(ELBOW_EN, ELBOW_LPWM, ELBOW_RPWM, ELBOW_SENSE);
  elbowJoint.encoder.initialize(ELBOW_POTENTIOMETER);

  gripper.initialize(GRIPPER_PIN);
  gripper.update();
}

void loadSettings()
{
  loadBoolParam(node, NULL, "debug", debug);

  baseJoint.loadSettings(node);
  shoulderJoint.loadSettings(node);
  elbowJoint.loadSettings(node);
}

void updateJoints(float timeStep)
{
  baseJoint.update(timeStep);
  shoulderJoint.update(timeStep);
  elbowJoint.update(timeStep);
  gripper.update();

  stateFeedback();

  if (debug)
  {
    rawFeedback();
  }
}

void velocityCommand(const str1ker::VelocityCommand& msg)
{
  baseJoint.writeVelocity(msg.base);
  shoulderJoint.writeVelocity(msg.shoulder);
  elbowJoint.writeVelocity(msg.elbow);
}

void positionCommand(const str1ker::PositionCommand& msg)
{
  baseJoint.writePosition(msg.base);
  shoulderJoint.writePosition(msg.shoulder);
  elbowJoint.writePosition(msg.elbow);
}

void gripperCommand(const str1ker::GripperCommand& msg)
{
  gripper.write(msg.holdTime);
}

void stateFeedback()
{
  stateFeedbackMsg.basePosition = baseJoint.getPosition();
  stateFeedbackMsg.baseVelocity = baseJoint.getVelocity();
  stateFeedbackMsg.baseCurrent = baseJoint.getCurrent();
  stateFeedbackMsg.baseStalled = baseJoint.isStalled();

  stateFeedbackMsg.shoulderPosition = shoulderJoint.getPosition();
  stateFeedbackMsg.shoulderVelocity = shoulderJoint.getVelocity();
  stateFeedbackMsg.shoulderCurrent = shoulderJoint.getCurrent();
  stateFeedbackMsg.shoulderStalled = shoulderJoint.isStalled();

  stateFeedbackMsg.elbowPosition = elbowJoint.getPosition();
  stateFeedbackMsg.elbowVelocity = elbowJoint.getVelocity();
  stateFeedbackMsg.elbowCurrent = elbowJoint.getCurrent();
  stateFeedbackMsg.elbowStalled = elbowJoint.isStalled();

  stateFeedbackMsg.voltage = supplySensor.readVoltage();
  stateFeedbackMsg.current = supplySensor.readCurrent();

  statePub.publish(&stateFeedbackMsg);
}

void rawFeedback()
{
  rawFeedbackMsg.base = baseJoint.encoder.raw();
  rawFeedbackMsg.shoulder = shoulderJoint.encoder.raw();
  rawFeedbackMsg.elbow = elbowJoint.encoder.raw();

  rawFeedbackMsg.baseI = baseJoint.motor.readRaw();
  rawFeedbackMsg.shoulderI = shoulderJoint.motor.readRaw();
  rawFeedbackMsg.elbowI = elbowJoint.motor.readRaw();

  rawPub.publish(&rawFeedbackMsg);
}

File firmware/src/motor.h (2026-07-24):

/*
                                                                                     ███████                  
 ████████████  ████████████   ████████████       █  █████████████  █           █  ███       ███  ████████████ 
█              █ █           █            █    █ █  █              █        ███      ███████    █            █
 ████████████  █   █         █████████████   █   █   █             █   █████      ███       ███ █████████████ 
             █ █     █       █            █      █    █            ████      █                  █            █
 ████████████  █       █     █            █      █      █████████  █          █   ███       ███ █            █
                                                                                     ███████                  
 motor.h
 BTS7960 Motor Driver: https://www.amazon.com/HiLetgo-BTS7960-Driver-Arduino-Current
 Copyright (C) 2025 Valeriy Novytskyy
 This software is licensed under GNU GPLv3
*/

#pragma once

/*----------------------------------------------------------*\
| Includes
\*----------------------------------------------------------*/

#include <ros.h>
#include "params.h"

/*----------------------------------------------------------*\
| Classes
\*----------------------------------------------------------*/

class Motor
{
public:
  static const int CURRENT_SENSE_UNUSED = -1;

  static constexpr float ADC_REFERENCE_VOLTS = 3.3f;
  static constexpr float ADC_MAX_COUNTS = 4095.0f;

  // BTS7960/IBT-2 current sense: I = V * (kILIS / R)
  static constexpr float CURRENT_SENSE_RESISTOR = 5100.0f;
  static constexpr float CURRENT_SENSE_KILIS = 8500.0f;
  static constexpr float CURRENT_SENSE_MULTIPLIER = CURRENT_SENSE_KILIS / CURRENT_SENSE_RESISTOR;

  static const unsigned int PWM_MAX = 255;
  static const unsigned int PWM_FREQ = 20000;

public:
  int lpwmPin;
  int rpwmPin;
  int isPin;
  int enPin;

  bool enabled;
  int pwmMin;
  int pwmMax;
  float stallThreshold;
  bool invert;
  bool stopBeforeReverse;

  float velocity;
  float current;
  int rawCurrent;

public:
  Motor():
    lpwmPin(0),
    rpwmPin(0),
    isPin(0),
    enPin(0),
    enabled(false),
    pwmMin(0),
    pwmMax(PWM_MAX),
    stallThreshold(1.0),
    invert(false),
    stopBeforeReverse(false),
    velocity(0.0),
    current(0.0),
    rawCurrent(0)
  {
  }

public:
  void initialize(
    int en,
    int lpwm,
    int rpwm,
    int is,
    int min = 0,
    int max = PWM_MAX,
    bool invertCommand = false,
    float stallCurrentThreshold = 1.0)
  {
    enPin = en;
    lpwmPin = lpwm;
    rpwmPin = rpwm;
    isPin = is;
    pwmMin = min;
    pwmMax = max;
    invert = invertCommand;
    stopBeforeReverse = false;
    stallThreshold = stallCurrentThreshold;
    velocity = 0.0;
    current = 0.0;

    pinMode(enPin, OUTPUT);
    digitalWrite(enPin, LOW);

    pinMode(lpwmPin, OUTPUT);
    pinMode(rpwmPin, OUTPUT);
    analogWriteFrequency(lpwmPin, PWM_FREQ);
    analogWriteFrequency(rpwmPin, PWM_FREQ);

    analogWrite(lpwmPin, 0);
    analogWrite(rpwmPin, 0);
  }

  void loadSettings(ros::NodeHandle& node, const char* group)
  {
    loadBoolParam(node, group, "enabled", enabled);
    loadParam(node, group, "pwmMin", pwmMin);
    loadParam(node, group, "pwmMax", pwmMax);
    loadParam(node, group, "stallThreshold", stallThreshold);
    loadBoolParam(node, group, "stopBeforeReverse", stopBeforeReverse);
    loadBoolParam(node, group, "invert", invert);

    if (pwmMin < 0 || pwmMin > int(PWM_MAX))
    {
      char buffer[100] = {0};
      snprintf(buffer, sizeof(buffer), "%s/pwmMin out of range [0..%u]: %d",
        group, PWM_MAX, pwmMin);
      node.logwarn(buffer);
    }

    if (pwmMax < 0 || pwmMax > int(PWM_MAX))
    {
      char buffer[100] = {0};
      snprintf(buffer, sizeof(buffer), "%s/pwmMax out of range [0..%u]: %d",
        group, PWM_MAX, pwmMax);
      node.logwarn(buffer);
    }

    if (pwmMin > pwmMax)
    {
      char buffer[100] = {0};
      snprintf(buffer, sizeof(buffer), "%s has pwmMin > pwmMax (%d > %d)",
        group, pwmMin, pwmMax);
      node.logwarn(buffer);
    }

    if (stallThreshold < 0.0f || stallThreshold > 1.0f)
    {
      char buffer[100] = {0};
      char threshold_s[16];
      dtostrf(stallThreshold, 0, 4, threshold_s);
      snprintf(buffer, sizeof(buffer), "%s/stallThreshold out of range [0..1]: %s",
        group, threshold_s);
      node.logwarn(buffer);
    }

    if (enabled)
    {
      enable();
    }
  }

  void enable()
  {
    enabled = true;
    digitalWrite(enPin, HIGH);
  }

  void disable()
  {
    enabled = false;
    digitalWrite(enPin, LOW);
    analogWrite(lpwmPin, 0);
    analogWrite(rpwmPin, 0);
    velocity = 0.0f;
  }

  float read()
  {
    if (isPin < 0)
    {
      rawCurrent = 0;
      current = 0.0f;
      return current;
    }

    rawCurrent = analogRead(isPin);
    float sensedVoltage = (float(rawCurrent) / ADC_MAX_COUNTS) * ADC_REFERENCE_VOLTS;
    current = sensedVoltage * CURRENT_SENSE_MULTIPLIER;
    return current;
  }

  int readRaw()
  {
    return rawCurrent;
  }

  void write(float command)
  {
    if (!enabled) return;

    float speed = constrain(abs(command), 0.0f, 1.0f);
    float direction = command >= 0 ? 1 : -1;

    if (invert)
    {
      direction *= -1;
    }

    int pwm = int(speed * float(PWM_MAX));

    if (pwm != 0)
    {
      if (pwm < pwmMin)
      {
        pwm = pwmMin;
      }
      else if (pwm > pwmMax)
      {
        pwm = pwmMax;
      }
    }

    float limitedSpeed = float(pwm) / float(PWM_MAX);
    float nextCommand = direction * limitedSpeed;

    bool reversedDirection =
      (velocity > 0.0f && nextCommand < 0.0f) ||
      (velocity < 0.0f && nextCommand > 0.0f);

    if (stopBeforeReverse && reversedDirection)
    {
      analogWrite(lpwmPin, 0);
      analogWrite(rpwmPin, 0);
      velocity = 0.0f;
      return;
    }

    if (nextCommand != velocity)
    {
      int lpwm = direction < 0 ? 0 : pwm;
      int rpwm = direction > 0 ? 0 : pwm;

      analogWrite(lpwmPin, lpwm);
      analogWrite(rpwmPin, rpwm);

      velocity = direction * limitedSpeed;
    }
  }

  void debug(ros::NodeHandle& node, const char* group)
  {
    char buffer[256] = {0};
    char thresh_s[16], current_s[16];

    dtostrf(stallThreshold, 0, 4, thresh_s);
    dtostrf(current, 0, 4, current_s);

    snprintf(buffer, sizeof(buffer),
      "%s: pwmMin=%d pwmMax=%d %s stallThreshold=%s current=%s%s%s",
      group, pwmMin, pwmMax,
      enabled ? "enabled" : "disabled",
      thresh_s, current_s,
      invert ? " invert" : "",
      stopBeforeReverse ? " stopBeforeReverse" : "");

    node.loginfo(buffer);
  }

};

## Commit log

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2020-03-17 Add frame and shuffle design:
    [face-scaled.ipt, frame.ipt]
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2020-03-19 Added top and bottom arm brackets
    [frame.ipt]
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2020-04-03 Adding brackets and reorg
    [Forearm.ipt, ShoulderBracket.ipt, ShoulderChestBracket.ipt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]
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2020-04-08 Replace with fixed rods
    [Chest.ipt, Robot.iam, ShoulderBracket.ipt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]
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2020-04-12 UpperArm redesign
    [Chest.ipt, ChestShoulderBracket - Copy.ipt, ChestShoulderBracket.ipt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]
2020-04-13 Work on actuator mounts
    [Forearm.ipt, Robot.iam, UpperArm.ipt]
2020-04-13 Arm redesign to fit actuators
2020-04-14 Upper arm another redesign attempt
    [Forearm.ipt, Robot.iam, UpperArm.ipt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]
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2020-04-15 Finish upper arm actuator
    [Robot.iam, UpperArm2.ipt]
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2020-04-16 Working on forearm connector
    [ChestShoulderBracket - Copy.ipt, Forearm.ipt, ForearmActuatorConnector.ipt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]
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2020-04-23 Flesh out shoulder brackets
    [Arm.iam, Forearm.ipt, Robot.iam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]
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2020-04-27 Upper arm top solution
    [Chest.ipt, Robot.iam, ShoulderBracket.ipt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]
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2020-05-06 Chest side shape redo
    [Chest.ipt, Pelvis.iam, Robot.iam]
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2020-05-17 Leg replace progress
    [Knee.ipt, UpperLeg.ipt, UpperLeg2.ipt]
2020-05-18 More work on legs
    [Knee.ipt, Leg.iam, LowerLeg.ipt]
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2020-06-07 Update torso final drive
    [TorsoMount.ipt, TorsoSpacer.ipt]
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2020-10-31 Added Arm Quarters and new Solenoid, Arm Hole Size
    [UpperArm-Quarter-Back.ipt, UpperArm-Quarter-Front.ipt]
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2020-12-12 Main model clean up
    [ForearmActuatorConnector.ipt, UpperArmActuatorBracket.ipt, UpperArmBracket.ipt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]
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2021-01-23 Move mech parts to /parts
    [Arm.iam, Chest.ipt, ChestPelvisConnector.ipt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]
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2021-06-18 Arm redesign and custom encoder
    [Arm.iam, Encoder.iam, Encoder.ipt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]
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2021-06-18 Ready for remote head work
    [robotface-final.ipt]
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2021-07-17 Face redesign almost done
    [1501-0006-0340.STEP, 1600-0410-0004.ipt, 2802-0004-0012_92095A480.ipt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]
2021-07-18 Arducam detail and muzzle mount
    [MuzzleHeadMount.ipt, ShaftD6-2100-0006-0200.ipt]
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2021-07-25 Nose cover and vac tubes
    [FaceTubeConnector.ipt, HeadTopConnector.ipt, NoseCover.ipt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]
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2021-08-13 Animation and cleanup complete
    [ForearmActuatorConnector.ipt, robotface.iam, round-eyes.stl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]
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2022-11-15 Fix build error in arduinoMicro.h
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2023-02-05 Fix compile errors after gpiod switch
    [pwmServo.cpp]
2023-02-05 Add basic real time error reporting
    [pwmServo.cpp]
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2023-03-09 Fix ADC reading averages
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2023-03-12 Fix compile errors in pwm ino
    [pwm.ino]
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2023-03-14 Fix message compile errors
    [motor.h]
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2023-03-15 Fix compile errors in PWM sketch
    [pwm.ino]
2023-03-15 Fix compile errors in ADC sketch
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2023-03-18 Exported arm parts for simulation
    [Encoder.ipt, EncoderBase.ipt, EncoderBody.ipt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]
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2023-03-18 Complete initial description export
    [Forearm.iam, Forearm.stl, ForearmBoundingBox.ipt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]
2023-03-19 First iteration of description finalized
    [ArmBase.iam, ArmBase.stl, ArmBaseBoundingBox.ipt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]
2023-03-19 Move parts to root
    [Arm.0044.iam, Arm.iam, ArmProto.0002.iam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]
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2023-03-20 Convert models to meters
    [ArmBase.stl, Drumstick.stl, Forearm.stl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]
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2023-03-20 Convert bounding boxes from mm to meters
    [ArmBaseBoundingBox.stl, ForearmBoundingBox.stl, ShoulderBoundingBox.stl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]
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2023-03-20 Add drumstick collision geometry
    [robot.urdf]
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2023-03-20 Fill in physical descriptions
    [robot.urdf]
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2023-03-20 Fix arm turning
    [robot.urdf]
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2023-03-20 Clean up unused files
    [Arm.0044.iam, ArmProto.0002.iam, Chest.0134.ipt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]
2023-03-20 Add actuator links and joints
    [robot.urdf]
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2023-03-24 Round of cleaning up urdf
    [robot.urdf]
2023-03-24 Re-exported shoulder with different origin
    [Shoulder.stl]
2023-03-24 Re-export upper arm actuator body 2in
    [UpperArmActuatorBody.stl]
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2023-03-25 Drumstick visual exported on wrong axis
    [Drumstick.stl]
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2023-03-25 Update collision stls
    [robot.urdf]
2023-03-26 Fix wrist limit
    [robot.urdf]
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2023-03-26 Shorten upper arm actuator body
    [UpperArmActuatorBody.stl, robot.urdf]
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2023-03-27 Revert "Lengthen forearm actuator"
    This reverts commit 52cb549178ae56ad37ba80106483dcd69fc9dd6b.
    [ForearmActuatorBody.stl, robot.urdf]
2023-03-27 Revert "Shorten upper arm actuator body"
    This reverts commit a84f4c9be8dbbe7efa7a3a994118b4b1107c95e8.
    [UpperArmActuatorBody.stl, robot.urdf]
2023-03-27 Shorten upper arm actuator to measured dims
    [UpperArmActuatorBase.iam, UpperArmActuatorBaseBoundingBox.ipt, UpperArmActuatorBody.stl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]
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2023-03-27 Update shoulder mimic based on upper arm actuator change
    [robot.urdf]
2023-03-28 Update elbow and shoulder limits from photo ref
    [robot.urdf]
2023-03-28 Update elbow and shoulder mimics based on new limits
    [robot.urdf]
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2023-03-28 Fix shoulder bounding box
    [Shoulder.iam, ShoulderBoundingBox.ipt, ShoulderBoundingBox.stl]
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2023-03-30 Add solenoid collision urdf
    [robot.urdf]
2023-03-30 Fix wrist x offset
    [robot.urdf]
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2023-04-07 Validate and fix issues
    [robot.urdf]
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2023-04-11 Attach effector collision
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2023-04-19 Prevent jarring wrap on mount angle
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2023-05-17 Re-aligned arm parts to X axis except actuators
    [ArmBase.iam, ArmBase.stl, ArmBaseBoundingBox.stl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]
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2023-07-08 Fix build errors
    [robot.urdf]
2023-07-08 First pass fixing urdf, need stl export again
    [robot.urdf]
2023-07-08 Export parts aligned to X axis rotating on Z
    [Arm.iam, ArmSolenoid.iam, ForearmActuatorBody.stl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]
2023-07-08 Fix joints after re-orientation
    [robot.urdf]
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2023-07-09 Fix prismatic axis
    [robot.urdf]
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2023-07-10 Fix joint indexing
2023-07-10 Fix mimic limits
    [robot.urdf]
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2023-07-25 Reset temporary controller configuration
    [gazebo-controllers.yaml]
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2023-07-25 Restore forearm actuator body collision hull
    [ForearmActuatorBodyBoundingBox.stl]
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2023-07-29 Fix base offset
    [robot.urdf]
2023-07-29 Clean up URDF after fixing inertia
    [robot.urdf]
2023-07-29 Fix export error and unpause
    [robot.urdf]
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2023-08-02 Undo visual offset on base link after re-export
    [robot.urdf]
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2023-08-03 Fill in center of gravity for all links
    [robot.urdf]
2023-08-03 Fix forearm cog
    [robot.urdf]
2023-08-03 Upper arm actuator body inertial fix
    [robot.urdf]
2023-08-03 Raise higher to avoid contact with ground
    [robot.urdf]
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2023-09-01 Reverse solenoid direction
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2023-10-04 Fix PWM width and frequency
    [analog.ino]
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2023-12-18 Fix compile errors for new classes
    [controllers.yaml]
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2023-12-18 Fix startup issues
    [controllers.yaml]
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2023-12-18 Fix config channel mapping
    [controllers.yaml]
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2023-12-19 Remove unused model and add chest cover concept
    [ChestFrame.stl, ControllerBoardCover.blend]
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2023-12-26 Publish joint states and do not publish infinity
    [hardware.yaml]
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2023-12-26 Move joint state controller config to moveit config
    [hardware.yaml]
2023-12-27 Fix solenoid not being published by gazebo_ros_control
    [robot.urdf]
2023-12-27 Fix comment
    [robot.urdf]
2023-12-27 Fix encoder channel
    [hardware.yaml]
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2024-01-16 Fix joint state not initialized
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2025-01-20 Fix compile errors switching from velocity to position control
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2025-01-20 Fix shoulder offset in URDF
    [robot.urdf]
2025-01-20 Fix shoulder offset after re-design
    [robot.urdf]
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2025-01-31 Comments no longer needed
    [arm.ino]
2025-02-07 All compile errors fixed
    [arm.ino, motor.h]
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2025-02-19 Redesign spine link
    [SpineLink.ipt]
2025-02-19 New chest frame redesign
    [ChestFrame.ipt]
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2025-04-03 Stop using dynamic reconfigure and EEPROM, load settings using parameter server
    [hardware.yaml]
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2025-09-27 Preparing for spine re-design and connection to chest
    [Spine.ipt]
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2025-10-21 Rename and resize leg parts for international shipping
    [Hip.ipt, HipCoverTop.ipt, Knee.ipt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]
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2025-10-26 Arm bracket final redesign and attaching front arms
    [ArmScapula.ipt, ArmWithBaseLeft.iam, ArmWithBaseRight.iam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]
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2025-11-09 Arm fixture and new circuit breaker
    [ArmDriver.iam, ArmFixture.iam, ArmFrontLeft.iam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]
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2025-12-17 Fixed LED footprint and re-exported
    [ArmRobotBoardTeensy-CuBottom.gbr, ArmRobotBoardTeensy-CuTop.gbr, ArmRobotBoardTeensy-EdgeCuts.gbr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]
2026-01-08 Correct missing connections and two LED resistors because LEDs were too dim
    [ArmRobotBoardTeensy-CuBottom.gbr, ArmRobotBoardTeensy-CuTop.gbr, ArmRobotBoardTeensy-EdgeCuts.gbr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]
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2026-01-26 Leg actuators replaced with Antuator
    [Leg.iam]
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2026-01-31 Fix hi-z (floating) pins for solenoid and PWM channel 1
    [ArmRobotBoardTeensy-CuBottom.gbr, ArmRobotBoardTeensy-CuTop.gbr, ArmRobotBoardTeensy-EdgeCuts.gbr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]
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2026-02-01 Split into leg and arm, finish arm encoder
    [885012206089.stp, 885342208002.step, ArmEncoderBoard.kicad_pcb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]
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2026-02-03 Neck redesign pre-final
    [Head.iam, HeadMount.ipt, NeckBase.ipt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]
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2026-02-05 Replace encoder boards
    [ArmBackLeft.iam, ArmBackRight.iam, ArmBase.iam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]
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2026-02-09 Wrong schematic title
    [LegEncoderBoard.kicad_sch]
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2026-02-13 Debug Arduino serial not working
    [actuator.h, arm.ino]
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2026-02-13 Fixing config reading and dumping
    [actuator.h, arm.ino, motor.h]
2026-02-14 Fix loading settings on ROS Serial node
    [actuator.h, arm.ino, motor.h]
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2026-02-15 Fix PID control bugs
    [actuator.h, arm.ino, motor.h]
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2026-03-24 Fix compile errors and make it work with Arduino in VSCode again
    [motor.h]
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2026-04-02 Debug and re-design leg encoder and leg robot board
    [ArmEncoderBoard-CuBottom.gbr, ArmEncoderBoard-CuTop.gbr, ArmEncoderBoard-EdgeCuts.gbr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]
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2026-04-18 Add OLED display, light bar, voltage and current sensors
    [AO3400A.step, LegRobotBoardTeensy.kicad_pcb, MainRobotBoardTeensy.kicad_pcb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]
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2026-04-19 Re-routing main board, found a mistake
    [MainRobotBoardTeensy.kicad_pcb, MainRobotBoardTeensy.kicad_sch]
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2026-04-21 Fix current sense reading
    [motor.h]
2026-04-22 Fix compile errors on Teensy firmware
    [stepperMotor.h]
2026-04-22 Fix more compile errors in firmware
    [arm.ino]
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2026-04-29 Add LED number displays to legs board and re-finalize
    [BOM-LegRobotBoardTeensy.csv, CR0603-FX-4701ELF.step, HT16K33A-28SSOP.step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]
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2026-04-30 Fix wrong SPI mode on AS5045
    [absoluteEncoder.h]
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2026-05-13 Fix audio board flipped audio jack pins
    [AudioBoardTeensy.kicad_pcb, AudioBoardTeensy.kicad_sch]
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2026-05-20 Re-order leg board with different LED control chip
    [BOM-LegRobotBoardTeensy.csv, HT16K33A-28SSOP.step, IS31FL3730-QFLS2-TR.step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]
2026-05-20 Clean up and re-modeling battery based on 3D scan
    [ChestBottomPanel.ipt, DepthCameraHousing.ipt, DepthSensor.iam]
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2026-05-26 Fix overlapping components on back panel
    [BreakerMount.ipt]
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2026-05-27 Finalize power diagram and draft back panel silk screen
    [BackPanelSilk.dwg]
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2026-05-29 Leg board re-do LED displays, main board prepare for re-routing
    [0603WAF2202T5E.step, LegRobotBoardTeensy.kicad_pcb, LegRobotBoardTeensy.kicad_sch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]
2026-05-29 Re-route main board after flipping battery meter and removing INA260
    [MainRobotBoardTeensy.kicad_pcb]
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2026-06-13 Re-do breaker mount with power hub and new AC receptacle
    [BreakerMount.ipt]
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2026-06-20 Fix main board documentation inconsistencies
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
